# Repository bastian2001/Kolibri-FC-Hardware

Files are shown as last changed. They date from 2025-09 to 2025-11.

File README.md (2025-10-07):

# RP2350 Flight Controller for FPV

This is the hardware part of the Kolibri Flight Controller. Currently there are two versions: A 30mm (V0.5) and a 20mm (V0.6) FC. They are both pretty similar in terms of features, and mostly differ in their form factor and ease of soldering, but also featurewise, they are slightly different. They both feature:

-   3-8S input voltage
-   RP2350 microcontroller
-   2.4GHz ELRS onboard
-   5V 2.5A, 10V 2.5A buck converters
-   Analog character based OSD similar to Betaflight/iNav
-   Barometer (STM LPS22HB)
-   Speaker driver up to VBat

They differ slightly:

-   Gyro: BMI270 (30mm), ICM-42688-P with separate LDO (20mm)
-   ELRS: Gemini with PA/LNA (30mm), only one antenna with no PA/LNA (20mm)
-   Blackbox: SD slot (30mm), 256MiB flash chip (20mm)
-   20mm has a switchable 10V rail, 30mm uses that pin for a current sensor

While the 30mm FC works really well, the 20mm FC is just ordered and completely untested. While most features are a size decision, I will probably phase out the BMI270 and switch over to the ICM-42688-P, and I'd count a switchable 10V rail as more important than a current sensor, so as long as a 2350 is used, I will probably do that in the future, too. An RP235xB (only feasible on 30mm FC) has more pins though and might offer more features down the line, too.

The firmware and configurator can be found [here](https://github.com/bastian2001/Kolibri-FC).

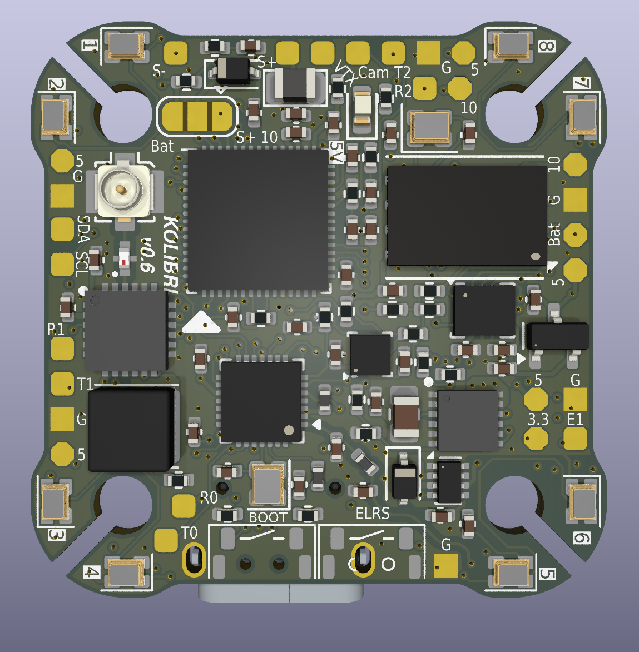
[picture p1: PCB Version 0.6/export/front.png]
Front side of FC

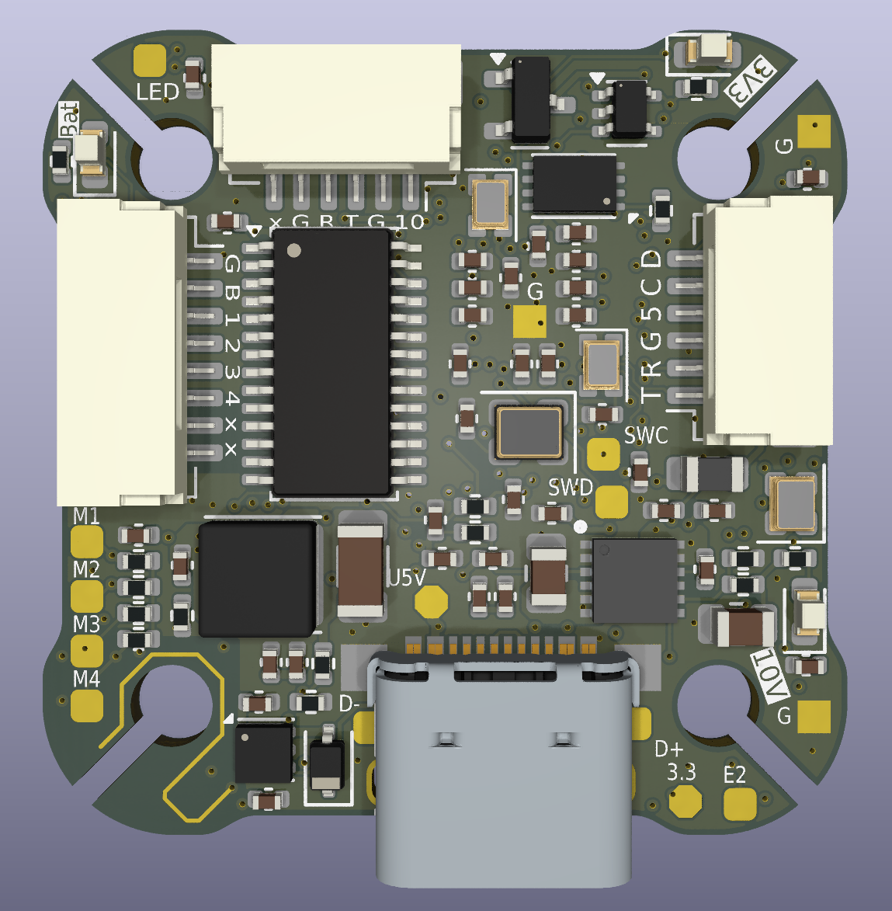
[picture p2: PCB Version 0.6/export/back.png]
Back side of FC


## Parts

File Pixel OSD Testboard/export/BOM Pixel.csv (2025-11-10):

# | Reference | Value | Footprint | Qty
1 | 'C1 | C2 | C3 | C4 | C5 | C6 | C7 | C8 | C9 | C10 | C14 | C15 | C16 | C19 | C20 | C22 | C28 | C45 | C46 | C54 | C56 | C57' | 100n | Capacitor_SMD:C_0402_1005Metric | 22
2 | 'C11 | C12' | 100n | Capacitor_SMD:C_0603_1608Metric_Pad1.08x0.95mm_HandSolder | 2
3 | C13 | 510p | Capacitor_SMD:C_0603_1608Metric_Pad1.08x0.95mm_HandSolder | 1
4 | 'C17 | C18 | C52' | 10u | Capacitor_SMD:C_0603_1608Metric_Pad1.08x0.95mm_HandSolder | 3
5 | 'C21 | C49 | C50 | C55' | 1u | Capacitor_SMD:C_0402_1005Metric | 4
6 | C23 | 10p | Capacitor_SMD:C_0402_1005Metric_Pad0.74x0.62mm_HandSolder | 1
7 | 'C24 | C25 | C26 | C27' | 100n | Capacitor_SMD:C_0402_1005Metric_Pad0.74x0.62mm_HandSolder | 4
8 | 'C29 | C30 | C31 | C32 | C33 | C34 | C35 | C36' | C | Capacitor_SMD:C_0201_0603Metric | 8
9 | 'C37 | C38 | C39 | C40 | C41 | C42 | C43 | C44' | C | Capacitor_SMD:C_0201_0603Metric_Pad0.64x0.40mm_HandSolder | 8
10 | 'C47 | C51' | 10u | Capacitor_SMD:C_0402_1005Metric | 2
11 | C48 | 10u | Capacitor_SMD:C_0603_1608Metric | 1
12 | C53 | 1u | Capacitor_SMD:C_0603_1608Metric_Pad1.08x0.95mm_HandSolder | 1
13 | D1 | 1N4148WS | Diode_SMD:D_SOD-323 | 1
14 | D2 | yellow | LED_SMD:LED_0603_1608Metric | 1
15 | D3 | green | LED_SMD:LED_0603_1608Metric | 1
16 | D4 | red | LED_SMD:LED_0603_1608Metric | 1
17 | D5 | SL16 | Diode_SMD:D_SOD-123 | 1
18 | J1 | USB_C_Receptacle_USB2.0_16P | Kolibri custom:USB-C SMD+THT | 1
19 | L1 | 10u | Inductor_SMD:L_0805_2012Metric | 1
20 | 'P1 | P2 | P3 | P4 | P5 | P6 | P7 | P8' | ~ | Kolibri custom:Solder_Pad_rounded | 8
21 | 'P9 | P10 | P11 | P12 | P13 | P14' | ~ | Kolibri custom:Solder_Pad_octa | 6
22 | 'P15 | P16 | P17 | P18' | ~ | Kolibri custom:Solder_Pad_rect | 4
23 | Q1 | 2SK3019 | Package_TO_SOT_SMD:SOT-523 | 1
24 | 'R1 | R2' | 5.1k | Resistor_SMD:R_0402_1005Metric | 2
25 | 'R3 | R4' | 27 | Resistor_SMD:R_0402_1005Metric | 2
26 | R5 | 680 | Resistor_SMD:R_0603_1608Metric_Pad0.98x0.95mm_HandSolder | 1
27 | R6 | 620 | Resistor_SMD:R_0603_1608Metric_Pad0.98x0.95mm_HandSolder | 1
28 | 'R7 | R9 | R11 | R13' | 33k | Resistor_SMD:R_0402_1005Metric_Pad0.72x0.64mm_HandSolder | 4
29 | 'R8 | R10 | R12 | R14' | 100k | Resistor_SMD:R_0402_1005Metric_Pad0.72x0.64mm_HandSolder | 4
30 | 'R15 | R39' | 1k | Resistor_SMD:R_0402_1005Metric | 2
31 | 'R16 | R27 | R36' | 10k | Resistor_SMD:R_0402_1005Metric | 3
32 | R18 | 100 | Resistor_SMD:R_0603_1608Metric_Pad0.98x0.95mm_HandSolder | 1
33 | 'R19 | R20' | 100k | Resistor_SMD:R_0603_1608Metric_Pad0.98x0.95mm_HandSolder | 2
34 | 'R22 | R23 | R24 | R25 | R26 | R43 | R44' | 1k | Resistor_SMD:R_0603_1608Metric_Pad0.98x0.95mm_HandSolder | 7
35 | 'R28 | R29' | 75 | Resistor_SMD:R_0402_1005Metric | 2
36 | 'R32 | R33' | 100k | Resistor_SMD:R_0402_1005Metric | 2
37 | R34 | 47k | Resistor_SMD:R_0402_1005Metric | 1
38 | R35 | 15k | Resistor_SMD:R_0402_1005Metric | 1
39 | 'R37 | R38' | 470 | Resistor_SMD:R_0402_1005Metric | 2
40 | R40 | 1M | Resistor_SMD:R_0603_1608Metric_Pad0.98x0.95mm_HandSolder | 1
41 | R41 | 2.2M | Resistor_SMD:R_0603_1608Metric_Pad0.98x0.95mm_HandSolder | 1
42 | R42 | 390k | Resistor_SMD:R_0603_1608Metric_Pad0.98x0.95mm_HandSolder | 1
43 | SW1 | ~ | Kolibri custom:Button C530669 | 1
44 | 'TP1 | TP2 | TP3 | TP4 | TP5 | TP6 | TP8 | TP9 | TP10' | TestPoint_Probe | TestPoint:TestPoint_Pad_D1.0mm | 9
45 | U1 | RP2040 | Package_DFN_QFN:QFN-56-1EP_7x7mm_P0.4mm_EP3.2x3.2mm | 1
46 | U2 | LM1881 | Package_SO:SOIC-8_3.9x4.9mm_P1.27mm | 1
47 | U3 | W25Q16JVSS | Package_SO:SOIC-8_5.3x5.3mm_P1.27mm | 1
48 | U4 | Opamp_Quad | Package_SO:TSSOP-14_4.4x5mm_P0.65mm | 1
49 | U5 | 74LVC1G66 | Package_TO_SOT_SMD:SOT-353_SC-70-5 | 1
50 | 'U6 | U10' | FSA3157P6X | Package_TO_SOT_SMD:SOT-363_SC-70-6 | 2
51 | U7 | TMUX1308DYY | Package_SO:Texas_DYY0016A_TSOT-23-16_2x4.2mm_P0.5mm | 1
52 | U8 | LGS5145 | Package_TO_SOT_SMD:SOT-23-6 | 1
53 | U9 | C19631737 | Package_TO_SOT_SMD:SOT-23-3 | 1
54 | U11 | OPA188xxDBV | Package_TO_SOT_SMD:TSOT-23-5 | 1
55 | Y1 | ASE-xxxMHz | Oscillator:Oscillator_SMD_Abracon_ASE-4Pin_3.2x2.5mm_HandSoldering | 1

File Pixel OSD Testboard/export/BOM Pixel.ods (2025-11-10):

# | Reference | Value | Footprint | Qty | LCSC # |  | Order # | Order Qty
1 | C1,C2,C3,C4,C5,C6,C7,C8,C9,C10,C14,C15,C16,C19,C20,C22,C28,C45,C46,C54,C56,C57 | 100n | Capacitor_SMD:C_0402_1005Metric | 22 | generic |  |  | 0
2 | C11,C12 | 100n | Capacitor_SMD:C_0603_1608Metric_Pad1.08x0.95mm_HandSolder | 2 | generic |  |  | 0
3 | C13 | 510p | Capacitor_SMD:C_0603_1608Metric_Pad1.08x0.95mm_HandSolder | 1 | generic |  | C20069830 | 100
4 | C17,C18,C52 | 10u | Capacitor_SMD:C_0603_1608Metric_Pad1.08x0.95mm_HandSolder | 3 | generic |  |  | 0
5 | C21,C49,C50,C55 | 1u | Capacitor_SMD:C_0402_1005Metric | 4 | generic |  |  | 0
6 | C23 | 10p | Capacitor_SMD:C_0402_1005Metric_Pad0.74x0.62mm_HandSolder | 1 | generic |  |  | 0
7 | C24,C25,C26,C27 | 100n | Capacitor_SMD:C_0402_1005Metric_Pad0.74x0.62mm_HandSolder | 4 | generic |  |  | 0
8 | C29,C30,C31,C32,C33,C34,C35,C36 | C | Capacitor_SMD:C_0201_0603Metric | 8 | generic test only |  | C7393836 | 100
9 | C37,C38,C39,C40,C41,C42,C43,C44 | C | Capacitor_SMD:C_0201_0603Metric_Pad0.64x0.40mm_HandSolder | 8 | generic test only |  | C7393836 | 0 | see above
10 | C47,C51 | 10u | Capacitor_SMD:C_0402_1005Metric | 2 | generic |  |  | 0
11 | C48 | 10u | Capacitor_SMD:C_0603_1608Metric | 1 | generic |  |  | 0
12 | C53 | 1u | Capacitor_SMD:C_0603_1608Metric_Pad1.08x0.95mm_HandSolder | 1 | generic |  |  | 0
13 | D1 | 1N4148WS | Diode_SMD:D_SOD-323 | 1 | generic |  |  | 0
14 | D2 | yellow | LED_SMD:LED_0603_1608Metric | 1 | generic |  |  | 0
15 | D3 | green | LED_SMD:LED_0603_1608Metric | 1 | generic |  |  | 0
16 | D4 | red | LED_SMD:LED_0603_1608Metric | 1 | generic |  |  | 0
17 | D5 | SL16 | Diode_SMD:D_SOD-123 | 1 | generic |  |  | 0
18 | J1 | USB_C_Receptacle_USB2.0_16P | Kolibri custom:USB-C SMD+THT | 1 | C963217 |  |  | 0
19 | L1 | 10u | Inductor_SMD:L_0805_2012Metric | 1 | generic 400mA |  | C285963 | 50
20 | P1,P2,P3,P4,P5,P6,P7,P8 | ~ | Kolibri custom:Solder_Pad_rounded | 8 | - |  |  | -
21 | P9,P10,P11,P12,P13,P14 | ~ | Kolibri custom:Solder_Pad_octa | 6 | - |  |  | -
22 | P15,P16,P17,P18 | ~ | Kolibri custom:Solder_Pad_rect | 4 | - |  |  | -
23 | Q1 | 2SK3019 | Package_TO_SOT_SMD:SOT-523 | 1 | generic, e.g. C41409350 |  | C41409350 | 50
24 | R1,R2 | 5.1k | Resistor_SMD:R_0402_1005Metric | 2 | generic 1% |  |  | 0
25 | R3,R4 | 27 | Resistor_SMD:R_0402_1005Metric | 2 | generic 1% |  |  | 0
26 | R5 | 680 | Resistor_SMD:R_0603_1608Metric_Pad0.98x0.95mm_HandSolder | 1 | generic 1% |  | C3016261 | 100
27 | R6 | 620 | Resistor_SMD:R_0603_1608Metric_Pad0.98x0.95mm_HandSolder | 1 | generic 1% |  | C49653145 | 100
28 | R7,R9,R11,R13 | 33k | Resistor_SMD:R_0402_1005Metric_Pad0.72x0.64mm_HandSolder | 4 | generic 1% |  |  | 0
29 | R8,R10,R12,R14 | 100k | Resistor_SMD:R_0402_1005Metric_Pad0.72x0.64mm_HandSolder | 4 | generic 1% |  |  | 0
30 | R15,R39 | 1k | Resistor_SMD:R_0402_1005Metric | 2 | generic 1% |  |  | 0
31 | R16,R27,R36 | 10k | Resistor_SMD:R_0402_1005Metric | 3 | generic 1% |  |  | 0
32 | R18 | 100 | Resistor_SMD:R_0603_1608Metric_Pad0.98x0.95mm_HandSolder | 1 | generic 1% |  |  | 0
33 | R19,R20 | 100k | Resistor_SMD:R_0603_1608Metric_Pad0.98x0.95mm_HandSolder | 2 | generic 1% |  |  | 0
34 | R22,R23,R24,R25,R26,R43,R44 | 1k | Resistor_SMD:R_0603_1608Metric_Pad0.98x0.95mm_HandSolder | 7 | generic 1% |  |  | 0
35 | R28,R29 | 75 | Resistor_SMD:R_0402_1005Metric | 2 | generic 1% |  |  | 0
36 | R32,R33 | 100k | Resistor_SMD:R_0402_1005Metric | 2 | generic 1% |  |  | 0
37 | R34 | 47k | Resistor_SMD:R_0402_1005Metric | 1 | generic 1% |  |  | 0
38 | R35 | 15k | Resistor_SMD:R_0402_1005Metric | 1 | generic 1% |  |  | 0
39 | R37,R38 | 470 | Resistor_SMD:R_0402_1005Metric | 2 | generic 1% |  |  | 0
40 | R40 | 1M | Resistor_SMD:R_0603_1608Metric_Pad0.98x0.95mm_HandSolder | 1 | generic 1% |  | C2907003 | 100
41 | R41 | 2.2M | Resistor_SMD:R_0603_1608Metric_Pad0.98x0.95mm_HandSolder | 1 | generic 1% |  | C48391814 | 100
42 | R42 | 390k | Resistor_SMD:R_0603_1608Metric_Pad0.98x0.95mm_HandSolder | 1 | generic 1% |  | C163911 | 100
43 | SW1 | ~ | Kolibri custom:Button C530669 | 1 | generic, e.g. C530669 |  |  | 0
44 | TP1,TP2,TP3,TP4,TP5,TP6,TP8,TP9,TP10 | TestPoint_Probe | TestPoint:TestPoint_Pad_D1.0mm | 9 | - |  |  | -
45 | U1 | RP2040 | Package_DFN_QFN:QFN-56-1EP_7x7mm_P0.4mm_EP3.2x3.2mm | 1 | C2040 |  |  | 0
46 | U2 | LM1881 | Package_SO:SOIC-8_3.9x4.9mm_P1.27mm | 1 | C518922 |  | C518922 | 2
47 | U3 | W25Q16JVSS | Package_SO:SOIC-8_5.3x5.3mm_P1.27mm | 1 | C131025, C82317 |  |  | 0
48 | U4 | Opamp_Quad | Package_SO:TSSOP-14_4.4x5mm_P0.65mm | 1 | C7463388 |  | C7463388 | 10
49 | U5 | 74LVC1G66 | Package_TO_SOT_SMD:SOT-353_SC-70-5 | 1 | C46553571 |  | C46553571 | 20
50 | U6,U10 | FSA3157P6X | Package_TO_SOT_SMD:SOT-363_SC-70-6 | 2 | C41431789 |  | C41431789 | 10
51 | U7 | TMUX1308DYY | Package_SO:Texas_DYY0016A_TSOT-23-16_2x4.2mm_P0.5mm | 1 | C2877584 |  | C2877584 | 5
52 | U8 | LGS5145 | Package_TO_SOT_SMD:SOT-23-6 | 1 | C5123971 |  | C5123971 | 5
53 | U9 | C19631737 | Package_TO_SOT_SMD:SOT-23-3 | 1 | C19631737 |  | C19631737 | 50
54 | U11 | OPA188xxDBV | Package_TO_SOT_SMD:TSOT-23-5 | 1 | C7463385 |  | C7463385 | 5
55 | Y1 | ASE-xxxMHz | Oscillator:Oscillator_SMD_Abracon_ASE-4Pin_3.2x2.5mm_HandSoldering | 1 |  |  |  | 0
 |  |  |  |  |  |  |  | -
 |  |  |  |  |  |  |  | -
 | FC V0.6 Order: | order will be combined, ignore for Pixel PCB |  |  |  |  |  | -
1 | C1,C3,C4,C5,C6,C7,C8,C9,C10,C16,C17,C18,C19,C20,C21,C23,C24,C27,C28,C30,C34,C40,C44,C45,C46,C48,C56,C65,C67,C70,C71,C76,C85,C86 | 100n | Capacitor_SMD:C_0402_1005Metric | 34 | generic |  |  | 0
2 | C2,C11,C12,C13 | 4.7u | Capacitor_SMD:C_0402_1005Metric | 4 | generic |  |  | 0
3 | C14,C15,C38,C39,C79,C80 | 15p | Capacitor_SMD:C_0402_1005Metric | 6 | generic NP0 |  |  | 0
4 | C22 | 2.2u | Capacitor_SMD:C_0402_1005Metric | 1 | generic |  | C12530 | 100
5 | C25,C42,C43,C87 | 10n | Capacitor_SMD:C_0402_1005Metric | 4 | generic |  |  | 0
6 | C26,C29,C33,C35,C63,C64,C73,C81,C83,C84 | 1u | Capacitor_SMD:C_0402_1005Metric | 10 | generic |  |  | 0
7 | C31,C36,C77,C78,C88 | 10u | Capacitor_SMD:C_0402_1005Metric | 5 | generic |  |  | 0
8 | C32,C37 | 1.5p | Capacitor_SMD:C_0402_1005Metric | 2 | generic NP0 |  |  | 0
9 | C41 | 470n | Capacitor_SMD:C_0402_1005Metric | 1 | generic |  |  | 0
10 | C66 | 47u | Capacitor_SMD:C_1206_3216Metric | 1 | generic 10V+ |  |  | 0
11 | C68,C69 | 4.7u | Capacitor_SMD:C_0805_2012Metric | 2 | generic 50V+ |  | C2903668 | 50
12 | C72 | 22u | Capacitor_SMD:C_0805_2012Metric | 1 | generic 25V+ |  |  | 0
13 | D1,D2,D3,D4,D5,D6,D7,D8,D9,D11 | ~ | Kolibri custom:WS2812B_1615 | 10 | generic |  |  | 0
14 | D10,D12,D13 | 1N4148WS | Diode_SMD:D_SOD-323 | 3 | generic |  |  | 0
15 | D14 | red | LED_SMD:LED_0603_1608Metric | 1 | generic |  |  | 0
16 | D15 | violet | LED_SMD:LED_0603_1608Metric | 1 | generic |  |  | 0
17 | D16 | blue | LED_SMD:LED_0603_1608Metric | 1 | generic |  |  | 0
18 | D17 | green | LED_SMD:LED_0603_1608Metric | 1 | generic |  |  | 0
19 | FL1 | 2450FM07D0034T | SamacSys_Parts:2450FM07D0034T | 1 | C2917726, C6054595, C2651081 |  | C2651081 | 30
20 | IC1 | SX1280IMLTRT | SamacSys_Parts:QFN50P400X400X100-25N-D | 1 | C2151551 |  | C2151551 | 10
21 | IC5,IC6 | LMR38025SDRRR | SamacSys_Parts:SON50P300X300X80-13N | 2 | C22405313 |  |  | 0
22 | J1 | USB_C_Receptacle_USB2.0_16P | Kolibri custom:USB-C SMD+THT | 1 | C963217 |  |  | 0
23 | J3 | Conn_Coaxial_Small | Connector_Coaxial:U.FL_Molex_MCRF_73412-0110_Vertical | 1 | C5137195 |  |  | 0
24 | J5 | Conn_01x08_MountingPin | Connector_JST:JST_SH_SM08B-SRSS-TB_1x08-1MP_P1.00mm_Horizontal | 1 | generic, e.g. C7433429 |  |  | 0
25 | J6,J7 | Conn_01x06_MountingPin | Connector_JST:JST_SH_SM06B-SRSS-TB_1x06-1MP_P1.00mm_Horizontal | 2 | generic, e.g. C2688763 |  |  | 0
26 | L1 | 3.3u | Kolibri custom:Abracon AOTA 0806 | 1 | C42411119 |  |  | 0
27 | L2 | 2.0n | Inductor_SMD:L_0402_1005Metric | 1 | generic for RF |  |  | 0
28 | L3 | 3.0n | Inductor_SMD:L_0402_1005Metric | 1 | generic for RF |  |  | 0
29 | L4 | 24n | Inductor_SMD:L_0402_1005Metric | 1 | generic |  |  | 0
30 | L5 | 15u | Inductor_SMD:L_0805_2012Metric | 1 | generic |  |  | 0
31 | L7,L8 | 4.7u | Inductor_SMD:L_Cenker_CKCS4020 | 2 | generic, e.g. C520275 |  |  | 0
32 | P1,P2,P3,P4,P5,P6,P7,P8,P9,P10,P11,P12,P13,P16,P17,P18,P19,P20,P21,P35,P36,P37,P38 | ~ | Kolibri custom:Solder_Pad_rounded | 23 | - |  |  | -
33 | P14,P22,P23,P24,P26,P27,P40,P42,P43 | ~ | Kolibri custom:Solder_Pad_rect | 9 | - |  |  | -
34 | P15,P25,P28,P29,P30,P31,P32,P33,P34,P39,P41 | ~ | Kolibri custom:Solder_Pad_octa | 11 | - |  |  | -
35 | Q1 | BSS138 | Package_TO_SOT_SMD:SOT-23 | 1 | generic |  |  | 0
36 | R1,R2 | 27 | Resistor_SMD:R_0402_1005Metric | 2 | generic 1% |  |  | 0
37 | R3 | 33 | Resistor_SMD:R_0402_1005Metric | 1 | generic 1% |  |  | 0
38 | R4,R21,R22,R23,R30,R33 | 1k | Resistor_SMD:R_0402_1005Metric | 6 | generic 1% |  |  | 0
39 | R5,R6 | 5.1k | Resistor_SMD:R_0402_1005Metric | 2 | generic 1% |  |  | 0
40 | R7,R8,R34,R35,R36,R37 | 6.8k | Resistor_SMD:R_0402_1005Metric | 6 | generic 1% |  |  | 0
41 | R9,R10,R16,R20,R27 | 10k | Resistor_SMD:R_0402_1005Metric | 5 | generic 1% |  |  | 0
42 | R13,R26 | 100k | Resistor_SMD:R_0402_1005Metric | 2 | generic 1% |  |  | 0
43 | R14 | 39k | Resistor_SMD:R_0402_1005Metric | 1 | generic 1% |  |  | 0
44 | R15 | 40.2k | Resistor_SMD:R_0402_1005Metric | 1 | generic 1% |  |  | 0
45 | R17 | 22.6k | Resistor_SMD:R_0402_1005Metric | 1 | generic 1% |  |  | 0
46 | R18 | 21.5k | Resistor_SMD:R_0402_1005Metric | 1 | generic 1% |  |  | 0
47 | R19 | 90.9k | Resistor_SMD:R_0402_1005Metric | 1 | generic 1% |  |  | 0
48 | R24,R25 | 75 | Resistor_SMD:R_0402_1005Metric | 2 | generic 1% |  |  | 0
49 | R28 | 8.2k | Resistor_SMD:R_0402_1005Metric | 1 | generic 1% |  |  | 0
50 | R29 | 3.3k | Resistor_SMD:R_0402_1005Metric | 1 | generic 1% |  |  | 0
51 | R31 | 2.2k | Resistor_SMD:R_0402_1005Metric | 1 | generic 1% |  |  | 0
52 | R41 | 22k | Resistor_SMD:R_0402_1005Metric | 1 | generic 1% |  |  | 0
53 | SW1,SW2 | ~ | Kolibri custom:Button C530669 wo holes | 2 | generic, e.g. C530669 |  |  | 0
54 | U1 | RP2350A | Kolibri custom:QFN-60_EP_7x7_Pitch0.4mm | 1 | C42411118 |  |  | 0
55 | U2 | C5250982 | Package_TO_SOT_SMD:SOT-23 | 1 | Generic 1.8V, 70dB, e.g. C5250982 |  | C5250982 | 50
56 | U3 | ESP8685-H4 | Package_DFN_QFN:QFN-28-1EP_4x4mm_P0.4mm_EP2.4x2.4mm | 1 | C4944062 |  | C4944062 | 5
57 | U4 | TPS2116DRL | Package_TO_SOT_SMD:SOT-583-8 | 1 | C22399676, C3235557 |  |  | 0
58 | U5 | AT7456E | Package_SO:HTSSOP-28-1EP_4.4x9.7mm_P0.65mm_EP2.75x6.2mm | 1 | C82351 |  |  | 0
59 | U6 | MT29F2G01ABAGDWB-IT:G | Package_SON:WSON-8-1EP_8x6mm_P1.27mm_EP3.4x4.3mm | 1 | C410863 |  | C410863 | 2
60 | U7 | TPS746-3.3DRV | Package_SON:WSON-6-1EP_2x2mm_P0.65mm_EP1x1.6mm | 1 | C2846784 |  |  | 0
61 | U8 | C3029047 | Package_TO_SOT_SMD:SOT-353_SC-70-5 | 1 | generic LMV321. e.g. C3029047 |  | C3029047 | 10
62 | U10 | W25Q16JVUXIQ | Package_SON:Winbond_USON-8-1EP_3x2mm_P0.5mm_EP0.2x1.6mm | 1 | C2843335 |  |  | 0
63 | U11 | LPS22HB | Package_LGA:ST_HLGA-10_2x2mm_P0.5mm_LayoutBorder3x2y | 1 | C94049 |  |  | 0
64 | U12 | ICM-42688-P | Package_LGA:LGA-14_3x2.5mm_P0.5mm_LayoutBorder3x4y | 1 | C1850418 |  | C1850418 | 0
65 | Y1 | Crystal_GND24 | Crystal:Crystal_SMD_2520-4Pin_2.5x2.0mm | 1 | generic 12 Mhz, e.g. C7294610 |  |  | 0
66 | Y2,Y4,Y5 | Crystal_GND24 | Crystal:Crystal_SMD_2016-4Pin_2.0x1.6mm | 3 | generic, 27MHz e.g. C18214311, 52MHz e.g. C3034316, 40MHz e.g.C37635335 | 27 | C18214311 | 0
 |  |  |  |  |  | 52 | C3034316 | 0
 |  |  |  |  |  | 40 | C37635335 | 0
 |  |  |  |  |  | 52 TCXO | C22434896 | 10

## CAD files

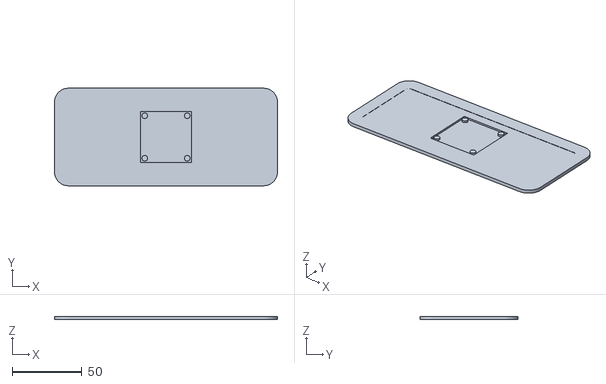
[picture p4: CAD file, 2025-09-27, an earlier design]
deprecated/PCB Version 0.1/Solder rig/Alignment card.stl
160.0 x 70.0 x 2.40

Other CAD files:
PCB Version 0.1/Solder rig/Alignment card.prt
deprecated/PCB Version 0.1/Solder rig/Alignment card.prt

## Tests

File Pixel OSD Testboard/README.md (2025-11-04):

# Goal of this board

I want to implement a pixel OSD in some future FC version. Because I am very unsure about how PAL/NTSC work, I want to test all of the hardware on a separate, cheap and easily debuggable, board first. It has a bunch of components that I want to remove later on, and that are just for debugging (thus making it larger than it needs to be). Furthermore, some of the hardware is chosen purely because I have it laying around (e.g. RP2040 instead of RP2350), so I get rid of old stock.

Pixel OSD will have multiple advantages

-   Drawing graphs and free shapes
-   varying font size and grid
-   cheaper
-   shades of grey (hopefully)
-   optional: remove grey, save one pin compared to MAX (hopefully)

This board is only a proof of concept. I'll try to put it into my quad during flight, but in the end it will be implemented on the main FC. Thus, it will likely only support a character based OSD, so it doesn't require a whole rewrite of the FC firmware for now: The interface is Serial/UART with MSP Displayport. Yes, hopefully this can give us a higher character count on regular analog video (to some extent, because the resolution is already close to its limit)

## Stuff that will be removed later on

-   Maybe I can buffer a bit less: 1-2 op amp channels could go?
-   Are all 100nF caps needed?
-   video LPF on LM1881 input?
-   Virtual white and the white selector: White should just come from the peak detector
-   Some components for lines like VSync: I want to use only composite sync
-   RP2040/LDO/LED/USB: Will be integrated into main RP2350 instead of MAX7456E

## How it works

How the hardware works is commented on the sheet.

The software will use PIO to detect sync pulses, then use DMA to feed a pixel buffer into the PIO which then outputs the data, timed correctly. PIO has the advantage of not needing super precise interrupt timing, because the coprocessor is very precise time-wise by definition.

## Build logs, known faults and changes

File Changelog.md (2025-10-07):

## Design errors, fixes and improvements between PCB revisions

### V0.1

-   Known issues:
    1. Current Sensor
        - If there is no current sensor wire attached, the INA139 will output 4.3V, killing the ADC and potentially the Microcontroller
        - Solution: Wire a pullup resistor from the C pad to the V+ pad to ensure that the measured current is 0 rather than infinity when there is nothing attached to the C pad.
    2. Buck Converters
        - A diode is misplaced, killing the buck converters
        - Solution: Place the diode in the correct spot on both bucks
    3. Oscillators
        - There is only a spot for crystals but not for their capacitors, and the wiring is wrong for use with oscillators
        - Solution: Change wiring for oscillator for the RP2040
    4. No pullup on the CS line for the flash
    5. Boot button flipped

### V0.2

-   Goal: A working PCB with some tests to make v0.3 the first final version
    -   It uses the same stencil as v0.1, hence I had to make some compromises with regards to routing and other best practices. I didn't want to spend another 15$ on a stencil, when PCBs are so cheap in comparison.
-   Fixes for all 5 problems with v0.1
-   Same stencil
-   Improvements:
    -   0402 solder bridges instead of 0603
    -   8 layers because that allows for free ENIG finish and POFV at JLCPCB
    -   put baro I2C on aux I2C of gyro? => Solder bridge to test this out

### V0.3

-   Goal: V0.2 (and from a purely flying performance perspective v0.1 too) was generally working very well. Goal is to put in some new features especially blackbox on the SD card due to the slow flash writing. Since the microSD has its own buffer, it should be much faster.
-   Improvements
    -   ELRS with true diversity built in
    -   SD card slot for blackbox
    -   new SPI barometer (Goertek SPL06-001)
    -   synchronous buck converters: smaller (, more efficient)
-   Fixes
    -   removed pullup on current sensor (A relic from the INA139)
-   Known issues
    -   100nF 0402 caps on the bottom layer are very close to each other, causing solder bridges - no issue but not ideal
    -   WiFi antenna poor range (5-10 cm), not sure why
    -   ELRS boot pad is hard to reach
    -   SX1281 crystals 90 degrees rotated --> SX1281 doesn't work at all (jank fix works)
    -   forgot I2C pullups. No issue rn (no sensors using I2C), but with a compass it might be
    -   Bad ELRS range --> a few possible reasons
        -   LNA not working --> most likely (yet reason still unknown), because the RSSI has a very fast jump from about -25 to -75dBm, indicating something else than a pure passives issue. Also, in the transmission path (telemetry), everything works fine, indicating that the PCB and passive components are fine in general
        -   pads grounded insufficiently --> my bad, I didn't compare the library footprint with the datasheet, some pads are not grounded, as they were marked NC in the library but GND in the datasheet --> I put a solder bridge on the pads that are not grounded, and still it doesn't work well, so still unlikely
        -   AT2401C just not working? --> unlikely, but maybe there's a difference between this clone and the RFX2401C
        -   All of them are pretty unlikely, given the weird jump, but I don't know what else it could be
    -   OSD crystal somewhat weird. Nothing I tried worked. I tried putting a crystal from a brand new off the shelf FC on it, as well as using a crystal from V0.2 (via separate wires), as well as changing various components like the AT7456E or capacitors. Sometimes (with the off-the-shelf crystal or the V0.2 crystal), I get video for like 20-60 seconds, but after a while they all stop working until I cut power and wait a few seconds. Nothing gets particularly warm, hence my confusion with the issue. Will go back to the design that worked in V0.2, to give me some space to play with all different sizes

### V0.4

-   Goal: V0.3 introduced a lot of new features, but not all work properly. This PCB will hopefully fix all the new issues that emerged with V0.3. Especially the ELRS range and the OSD crystal, but also implement a proper non-jank fixes for the other stuff. No new features, similar to V0.2 compared to V0.1. Biggest issue is that this time I cannot really explain to myself the two big issues and so I just have to guess.
-   Fixes (at least I hope)
    -   ELRS range -> Test RFX2401C instead of AT2401C, and ground all the pins. I will also swap the RFX2401C onto V0.3 after arrival to see if it's a PCB issue or a component issue
    -   ELRS WiFi -> proper filter according to datasheet
    -   ELRS crystal 90° rotated
    -   ELRS boot pad is now a button
    -   A pair of 4.7kOhm pullups for I2C
    -   OSD crystal -> back to V0.2 design, except with more possibilities of testing, like selectable voltage and selectable whether a crystal or oscillator is used
    -   slightly more spacing for 100nF caps on the bottom layer

### V0.5

-   Changes
    -   Switch to RP2350
    -   some changes to the ELRS receiver, maybe it'll work this time?
    -   First version designed in KiCad
    -   Bus layout changed:
        -   Dedicated 3-wire SPI for gyro (PIO) => DMA polling should be possible now
        -   baro has one I2C with external devices like compass
        -   SDIO for SD card (PIO)
        -   Dedicated SPI for OSD
    -   WS2812 LEDs for the swag
    -   better speaker driver
-   What works: Seemingly everything :tada:
-   Idea dump for future:
    -   Reorder 6 pin for GPS/compass: Currently not immediately compatible with Walksnail M10 (RX/TX and SDA/SCL need to be swapped)
    -   RP235xB: more pins for
        -   normal LEDs again
        -   full duplex spi to gyro
        -   separate external I2C for compass
        -   baro via SPI instead of I2C (together with OSD)
        -   more UARTs via PIO (once SPI is separated, pio2 is completely free)
        -   PWM outputs
    -   Speaker driver with optional 5V input for bench testing or in general
    -   more capacitance on 10V rail
    -   separate gyro LDO, or LPF on its supply
    -   custom pixel OSD using PIO/HSTX :thinking:
    -   possible space savings
        -   smaller crystals
        -   2354 instead of 2350 (no separate flash required)
        -   replace USB on SH plug with solder pads [optionally under the USB port]
        -   (pixel OSD instead of AT7456E)

### V0.6

-   Changes compared to V0.5
    -   ELRS
        -   from TD with PA/LNA to single without PA/LNA
        -   from ESP32 to ESP8685 (C3)
        -   No more separate LDO
    -   Gyro from BMI270 to ICM-42688-P with external clock
    -   Blackbox from SD slot to 2GBit flash chip
    -   Separate gyro LDO (1.8V – let's experiment!)
    -   USB
        -   remove JST header in favor of solder pads
        -   remove TVS
    -   shrink Crystal footprints
    -   replace current sensor pin with 10V reg switch

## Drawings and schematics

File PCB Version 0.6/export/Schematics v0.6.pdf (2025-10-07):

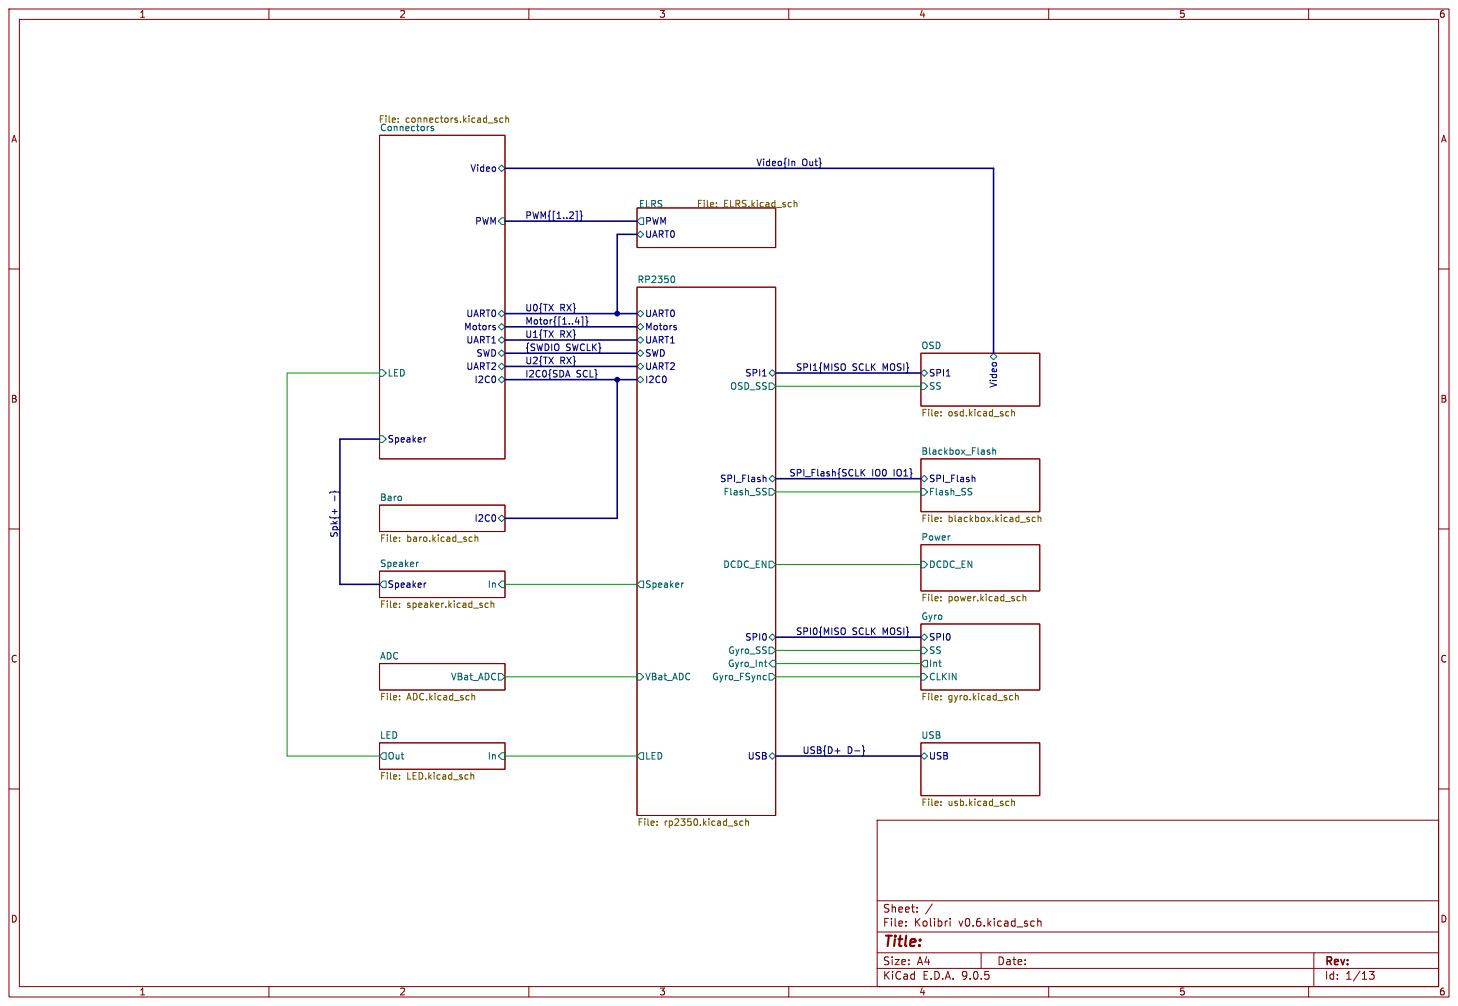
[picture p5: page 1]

Motor{[1..4]}
{SWDIO SWCLK}
SPI_Flash Blackbox_Flash File: blackbox.kicad_sch U2{TX RX}
I2C0{SDA SCL}

Id: 1/13 Title: File: Kolibri v0.6.kicad_sch Sheet: /DCDC_EN

Int CLKIN Gyro File: gyro.kicad_sch

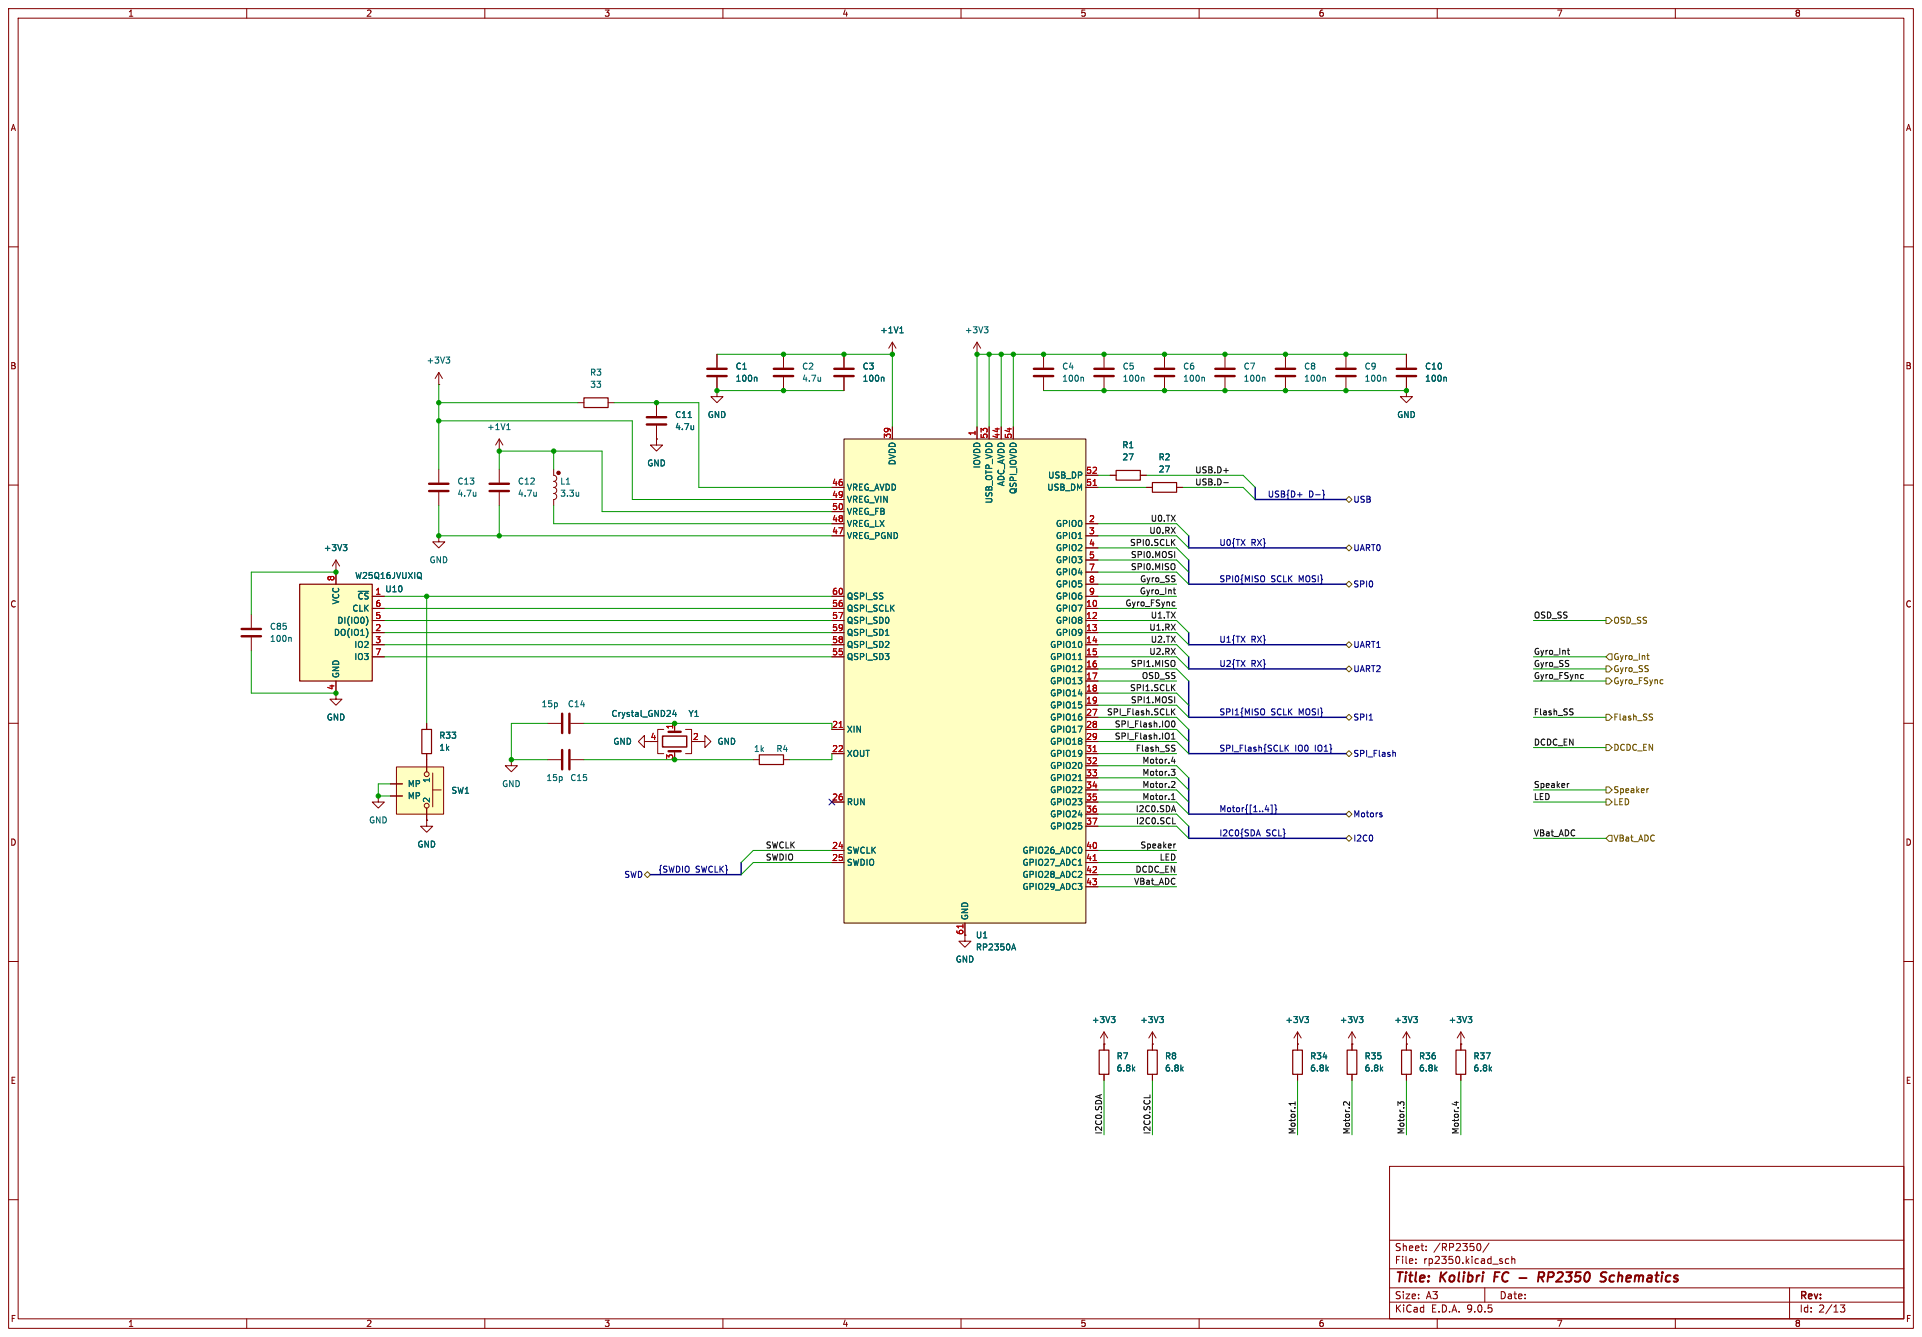
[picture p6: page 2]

File: rp2350.kicad_sch Sheet: /RP2350/
Id: 2/13 Title: Kolibri FC - RP2350 Schematics

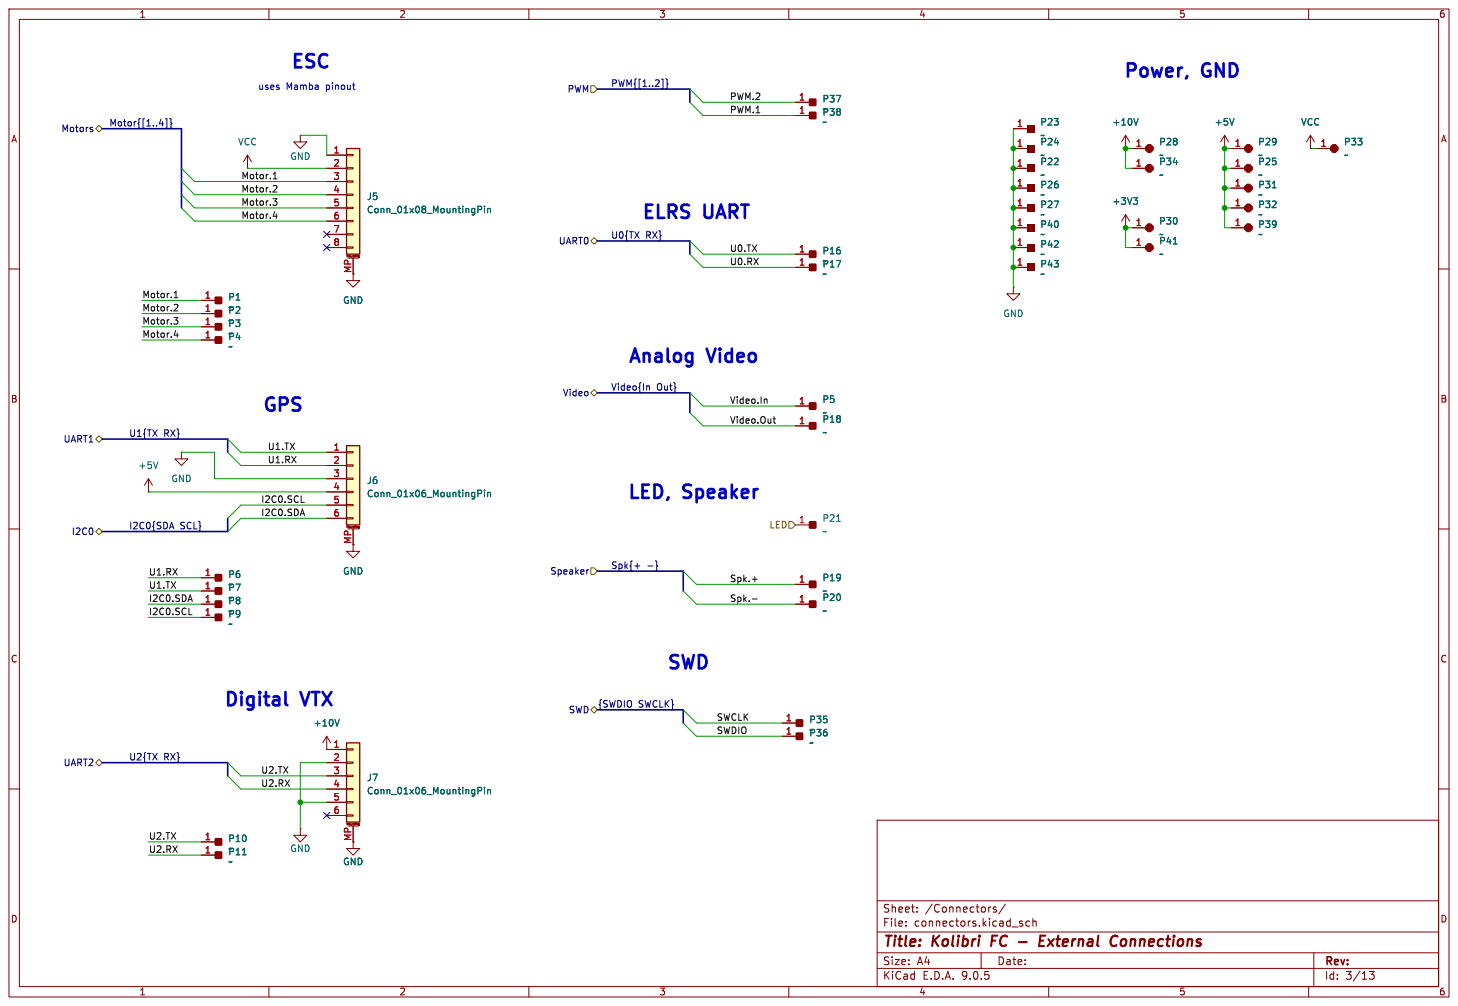
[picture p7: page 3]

Spk.+ Motor.1 Motor.2 Motor.3

File: connectors.kicad_sch Sheet: /Connectors/
Id: 3/13 Title: Kolibri FC - External Connections

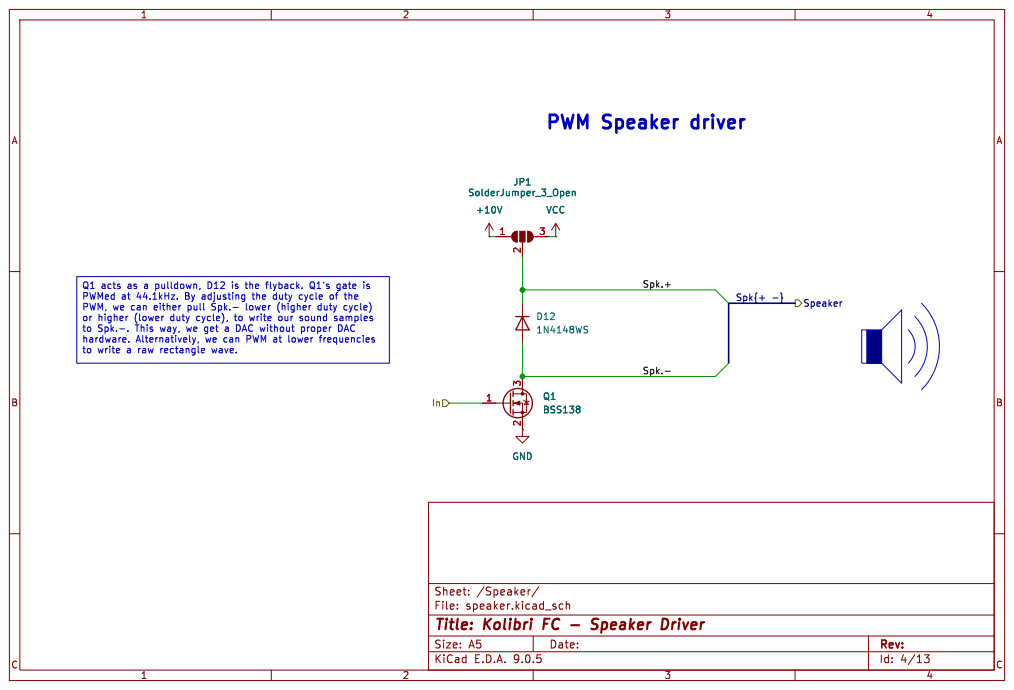
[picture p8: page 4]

JP1 SolderJumper_3_Open

Id: 4/13 Title: Kolibri FC - Speaker Driver File: speaker.kicad_sch Sheet: /Speaker/ 1

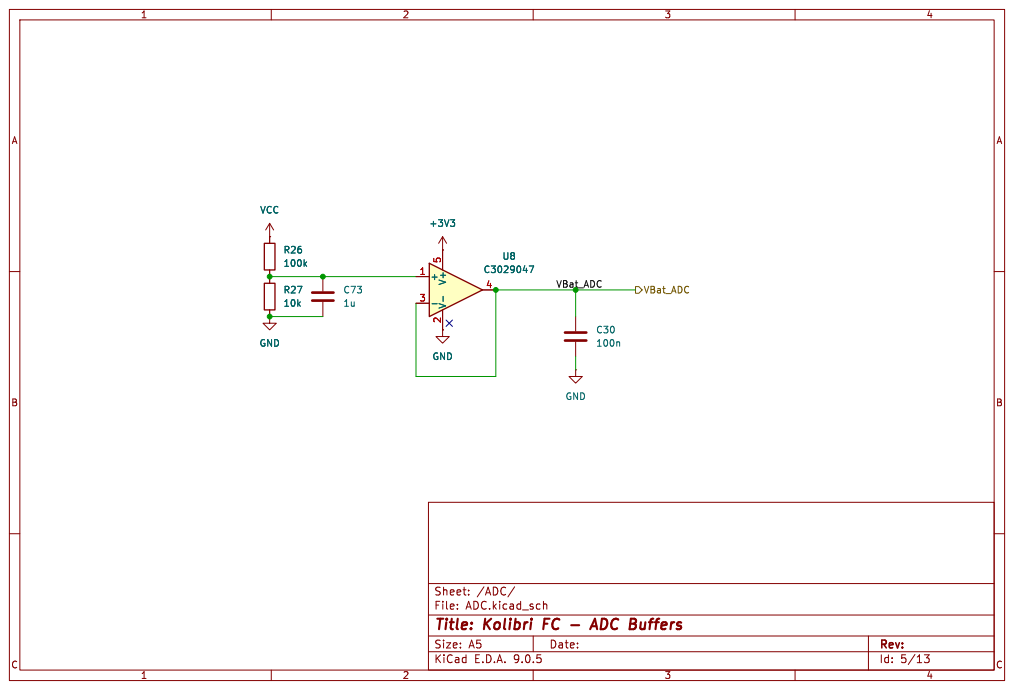
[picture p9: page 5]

Id: 5/13 Title: Kolibri FC - ADC Buffers

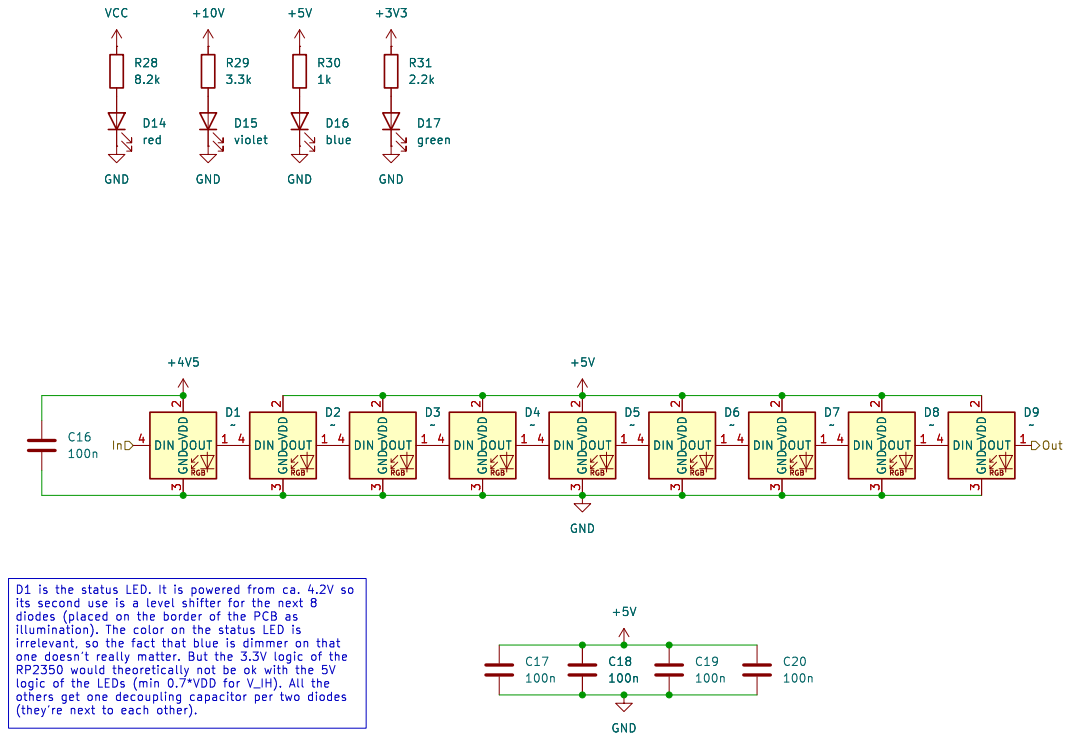
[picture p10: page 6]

its second use is a level shifter for the next 8

File: LED.kicad_sch Sheet: /LED/ C18

logic of the LEDs (min 0.7*VDD for V_IH). All the

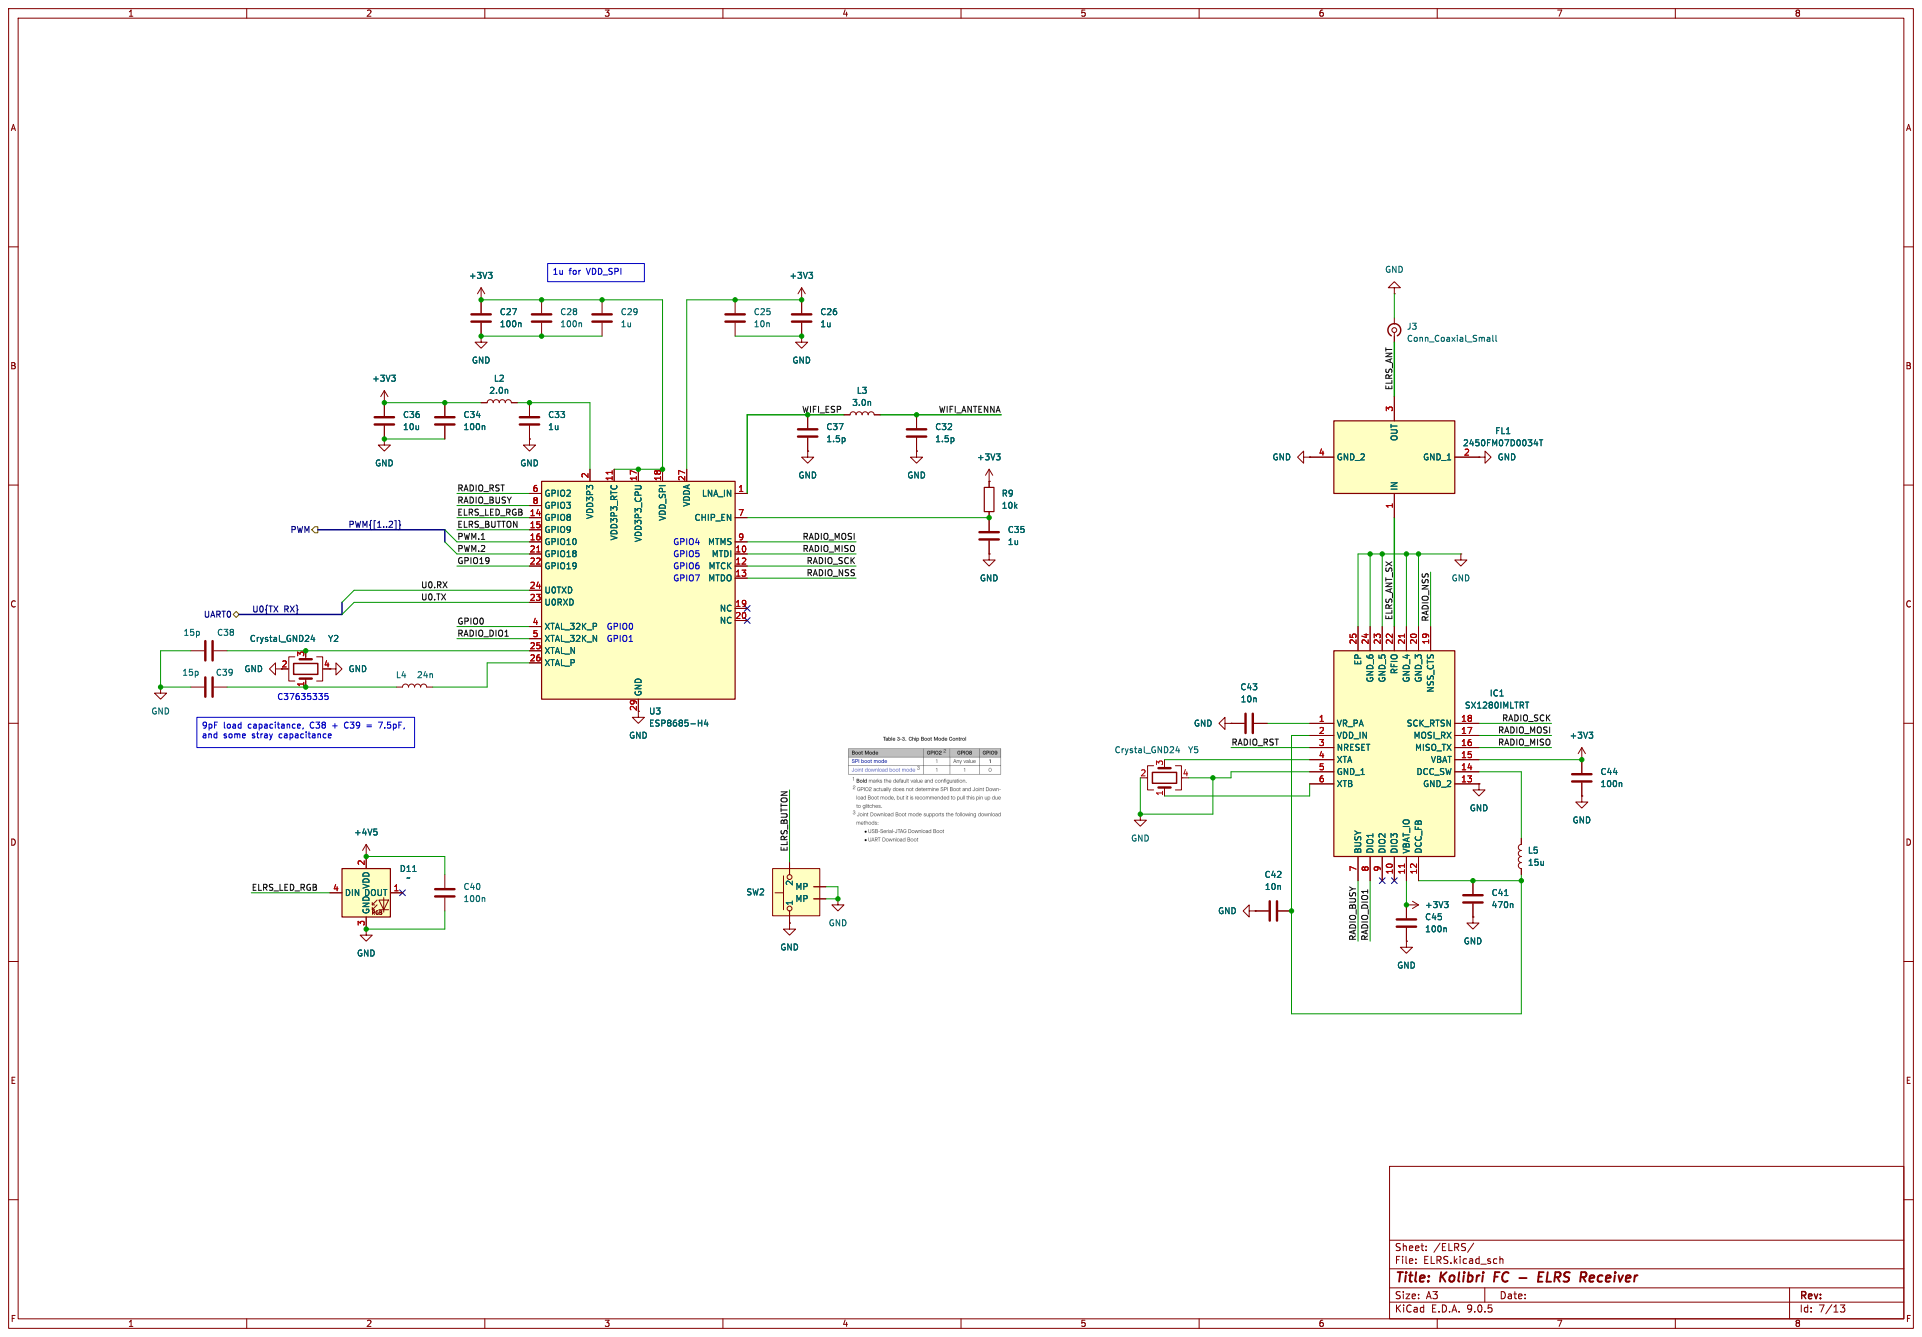
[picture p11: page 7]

LNA_IN 1 CHIP_EN 7 MTMS 9 MTDI 10 MTCK 12 MTDO 13 NC 19 NC 20 U3ESP8685-H4

3 GND GND GND GND

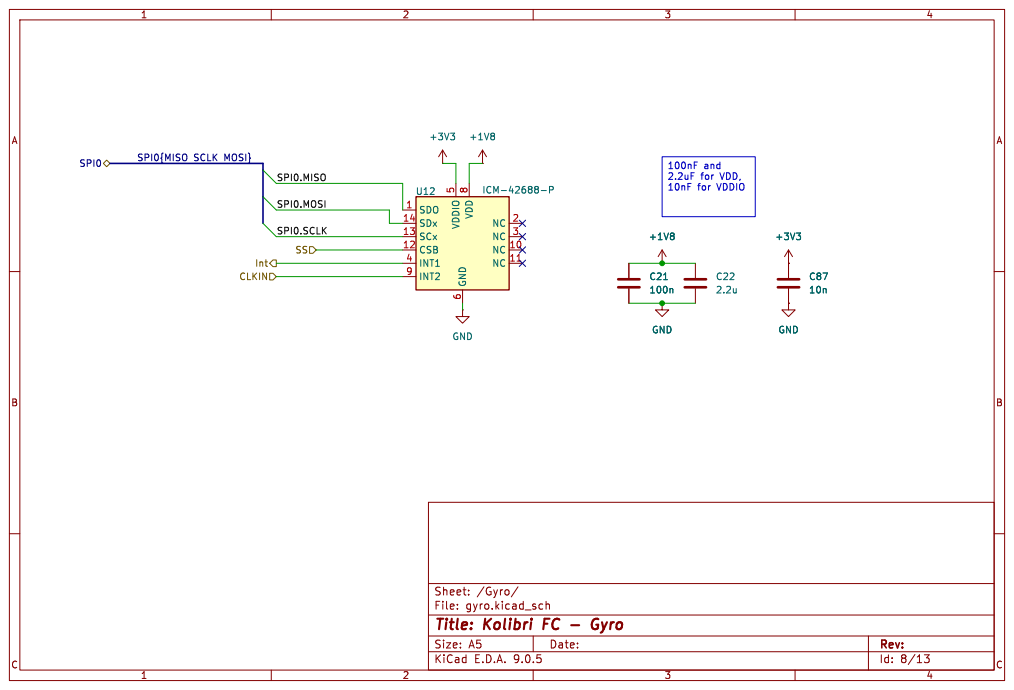
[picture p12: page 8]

8 NC 2 NC 3 NC 10 NC 11 U12 ICM-42688-P GND GND

2.2uF for VDD, 10nF for VDDIO

Id: 8/13 Title: Kolibri FC - Gyro

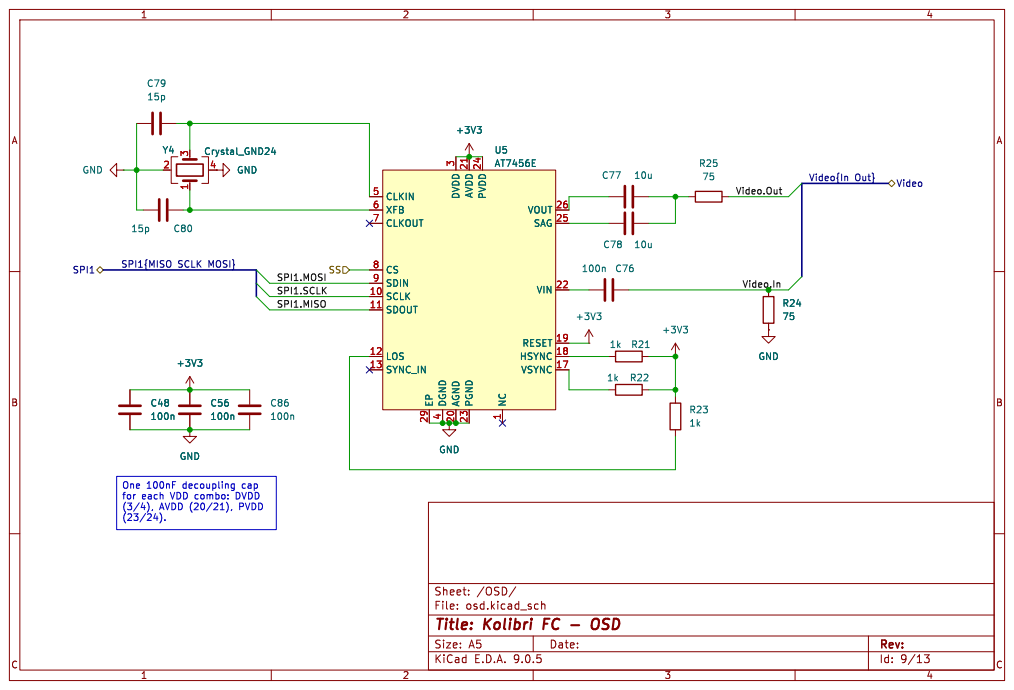
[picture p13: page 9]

1 VOUT 26 SAG 25 VIN 22 RESET 19 HSYNC 18 VSYNC 17 U5AT7456E

3 AGND 20 AVDD 21 PGND 23 PVDD 24 NC

1 VOUT 26 SAG 25 VIN 22 RESET 19 HSYNC 18 VSYNC 17 GND

for each VDD combo: DVDD

Id: 9/13 Title: Kolibri FC - OSD

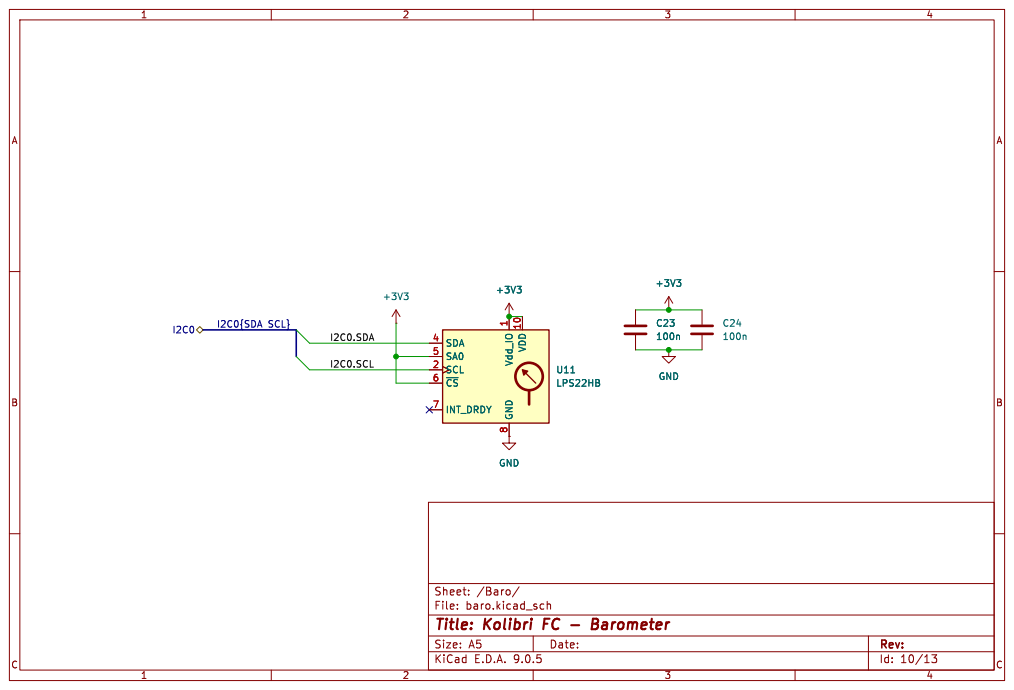
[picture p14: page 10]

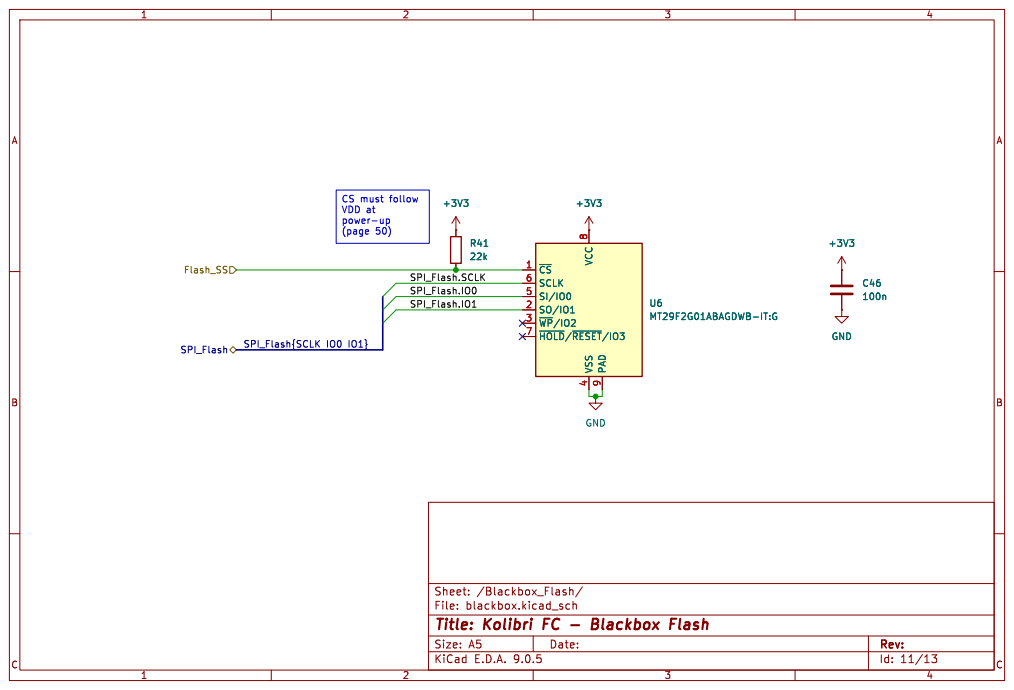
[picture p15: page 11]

SPI_Flash.IO0 CS must follow
VDD at power-up

Id: 11/13 Title: Kolibri FC - Blackbox Flash

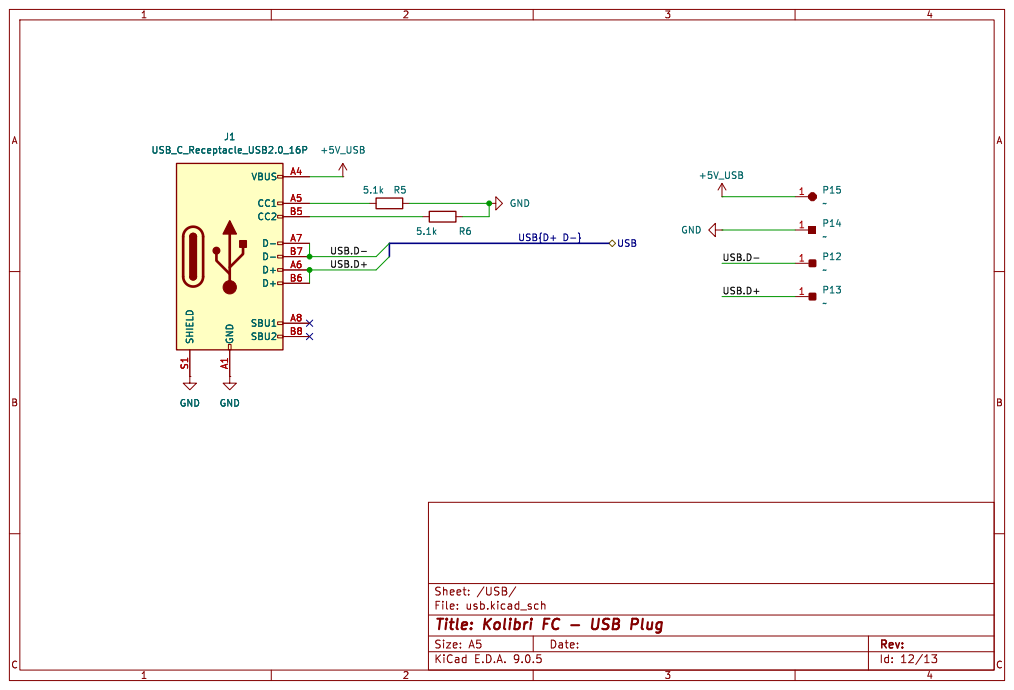
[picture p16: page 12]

File: usb.kicad_sch Sheet: /USB/
Id: 12/13 Title: Kolibri FC - USB Plug


Emergency diode for if that happens during flight.

File: power.kicad_sch Sheet: /Power/
Id: 13/13 Title: Kolibri FC - DCDC + LDO










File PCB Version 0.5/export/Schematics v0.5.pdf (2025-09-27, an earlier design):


I2C0 Baro File: baro.kicad_schVideo UART0 Motors
Gyro_Int SWD

Int Gyro File: gyro.kicad_sch

Id: 1/13 Title: File: Kolibri v0.5.kicad_sch Sheet: /


{SWDIO SWCLK} U10 W25Q16JVUXIQ
IO3 7 VCC
~{CS}1 CLK 6 DI(IO0) 5 DO(IO1) 2

SPI1{MISO SCLK MOSI} SPI1.SCLK

Id: 2/13 Title: Kolibri FC - RP2350 Schematics


ELRS PWM outputs
Video.Out PWM.2 PWM.4
PWM.3 SWDIO

Video.In PWM.1 U0.TX U0.RX

File: connectors.kicad_sch Sheet: /Connectors/ GND

Id: 3/13 Title: Kolibri FC - External Connections


JP1 SolderJumper_3_Open

Id: 4/13 Title: Kolibri FC - Speaker Driver File: speaker.kicad_sch Sheet: /Speaker/ 1


File: ADC.kicad_sch Sheet: /ADC/ R27

Id: 5/13 Title: Kolibri FC - ADC Buffers


File: LED.kicad_sch Sheet: /LED/ +5V D14

its second use is a level shifter for the next 8

logic of the LEDs (min 0.7*VDD for V_IH). All the


1u caps for VDD_SDIO and VDDA (pin 43 or 46), 100n for all other pins
U0.TX RADIO_SCK RADIO_MOSI
LED_RGB RADIO_MISO

1 2 MP MP SW2 GND GND


between VDDIO
and GNDIO and
one between VDD and GND

7 ASDx 2 ASCx 3 OCSB 10 OSDO 11 U2BMI270 C21

7 ASDx 2 ASCx 3 OCSB 10 OSDO 11 +3V3

Id: 8/13 Title: Kolibri FC - Gyro


1 VOUT 26 SAG 25 VIN 22 RESET 19 HSYNC 18 VSYNC 17 U5AT7456E

3 AGND 20 AVDD 21 PGND 23 PVDD 24 NC

1 VOUT 26 SAG 25 VIN 22 RESET 19 HSYNC 18 VSYNC 17 GND

for each VDD combo: DVDD

Id: 9/13 Title: Kolibri FC - OSD



File: sd.kicad_sch Sheet: /SD/
Id: 11/13 Title: Kolibri FC - Blackbox Micro SD


5 2 U8 WE-TVS-824015043 GND GND GND SHIELD S1 GND A1 VBUS A4 CC1 A5 CC2 B5 D- A7 D- B7 D+ A6 D+ B6 SBU1 A8 SBU2 B8

File: usb.kicad_sch Sheet: /USB/
Id: 12/13 Title: Kolibri FC - USB Plug


Emergency diode for if that happens during flight.

1 VOUT 2 ST 8 GND GND

separate 3.3V supply. Both LDOs have an almost identical pinout where only PG and GND are swapped, but because both

File: power.kicad_sch Sheet: /Power/
Id: 13/13 Title: Kolibri FC - DCDC + LDO

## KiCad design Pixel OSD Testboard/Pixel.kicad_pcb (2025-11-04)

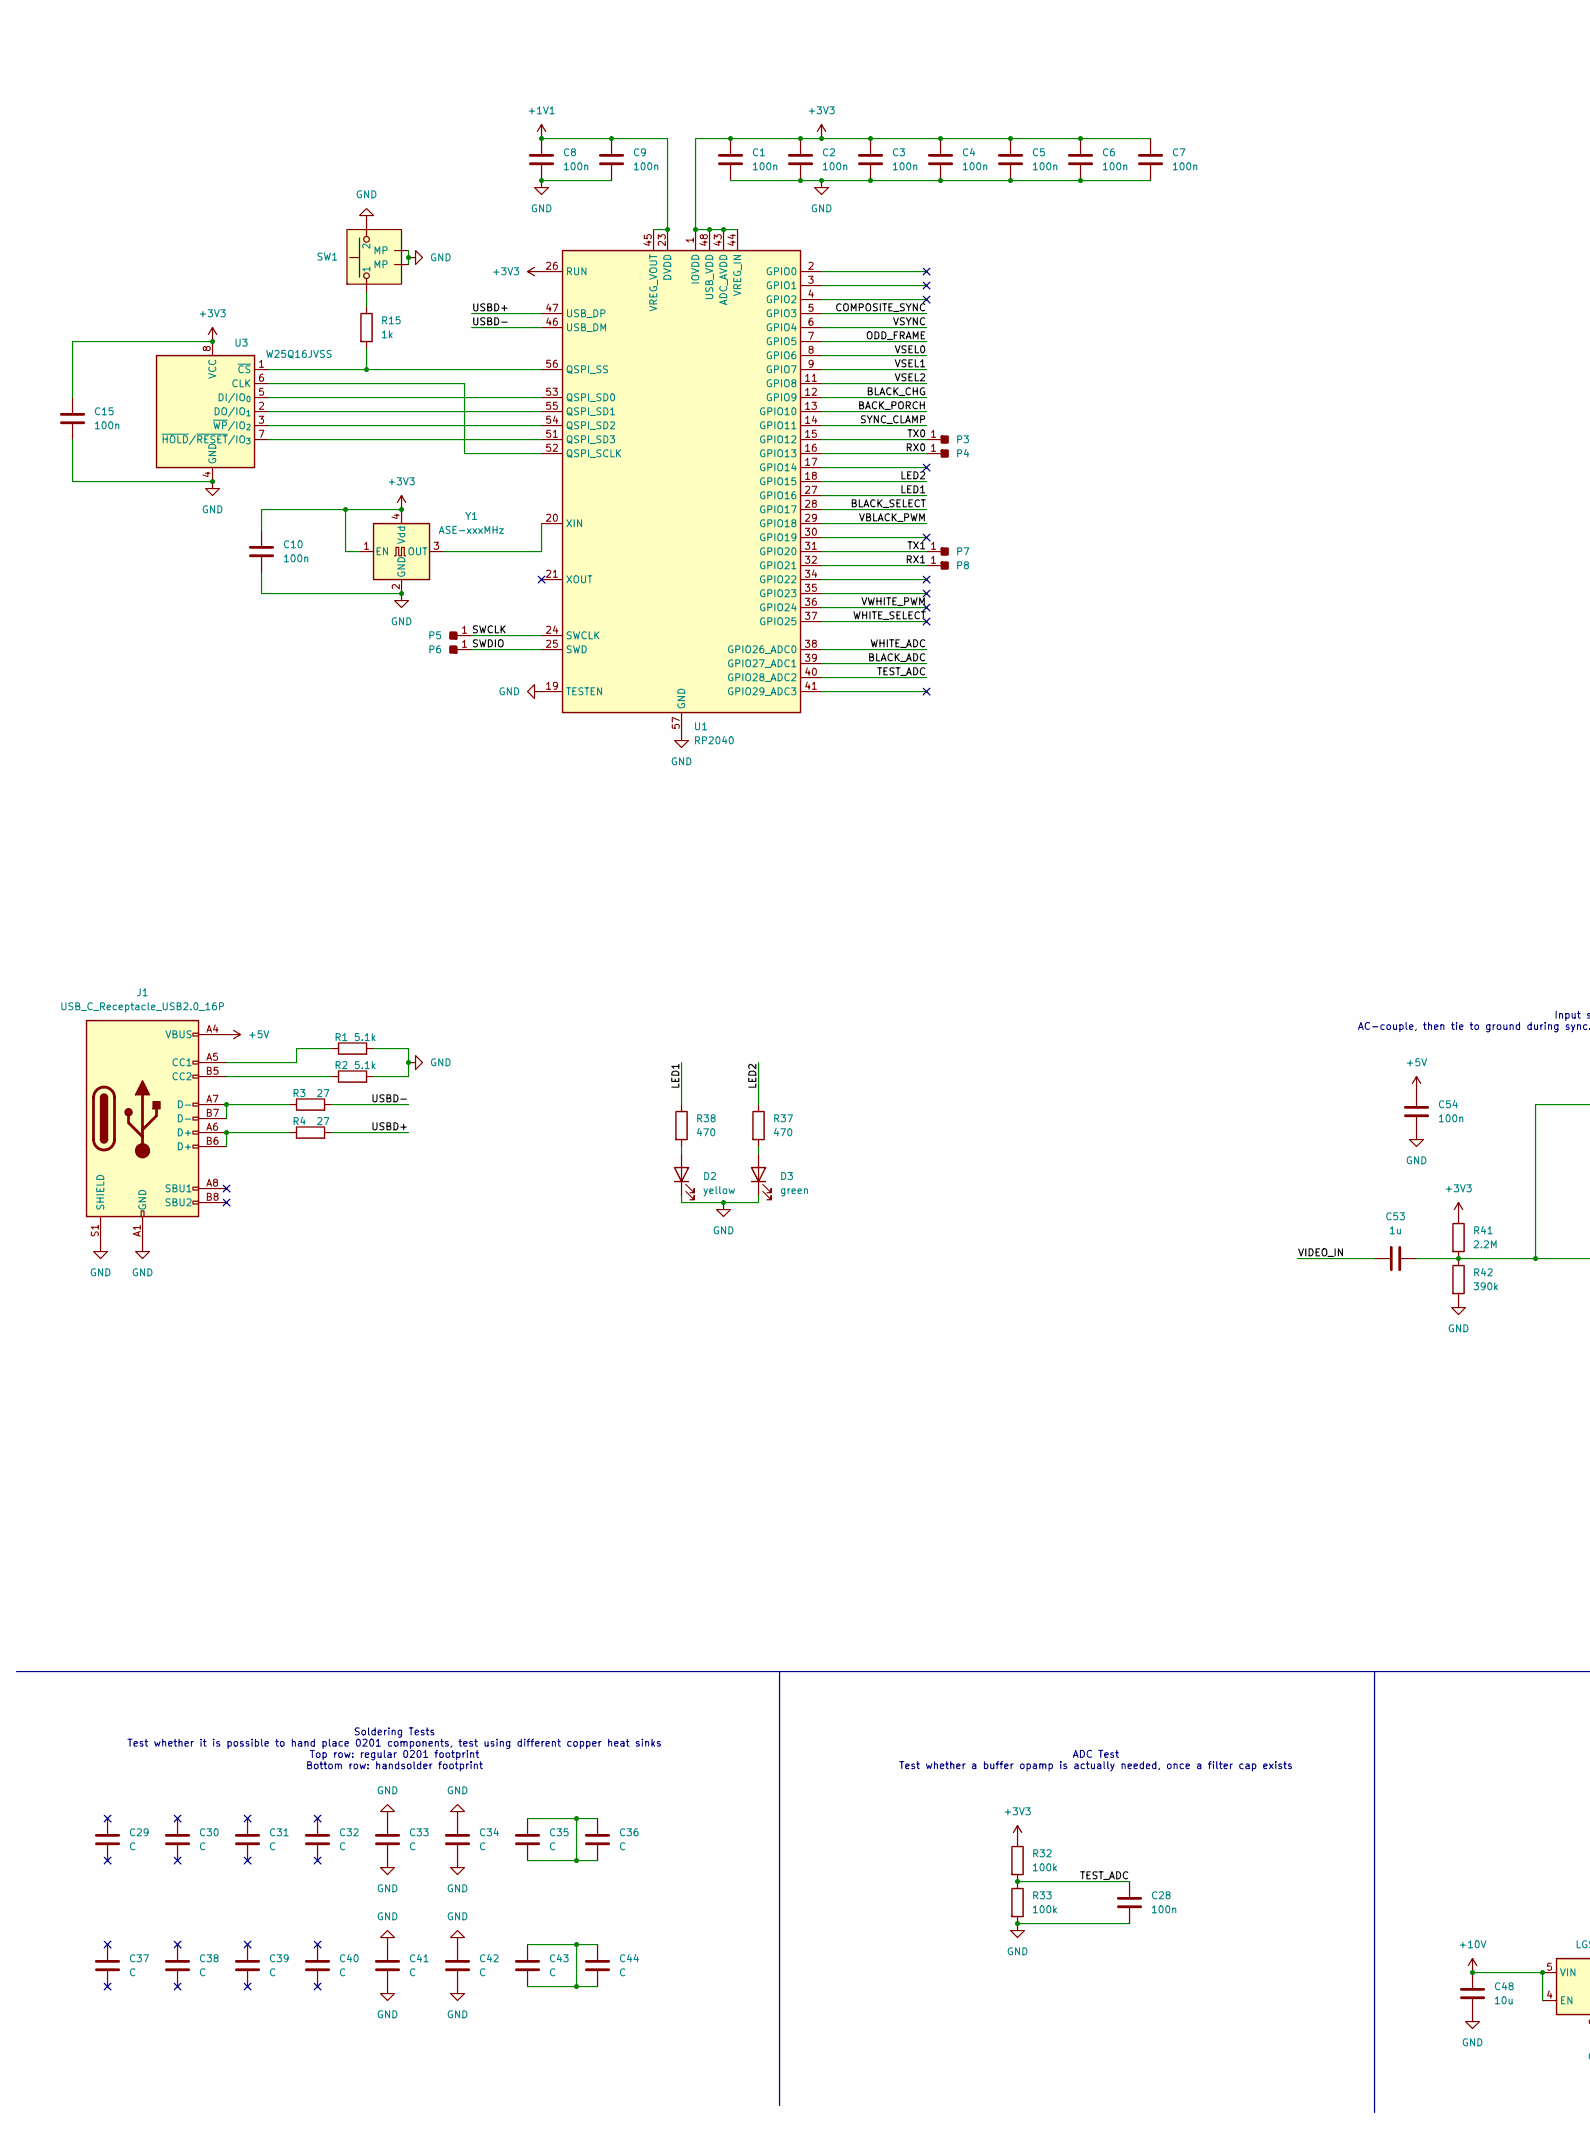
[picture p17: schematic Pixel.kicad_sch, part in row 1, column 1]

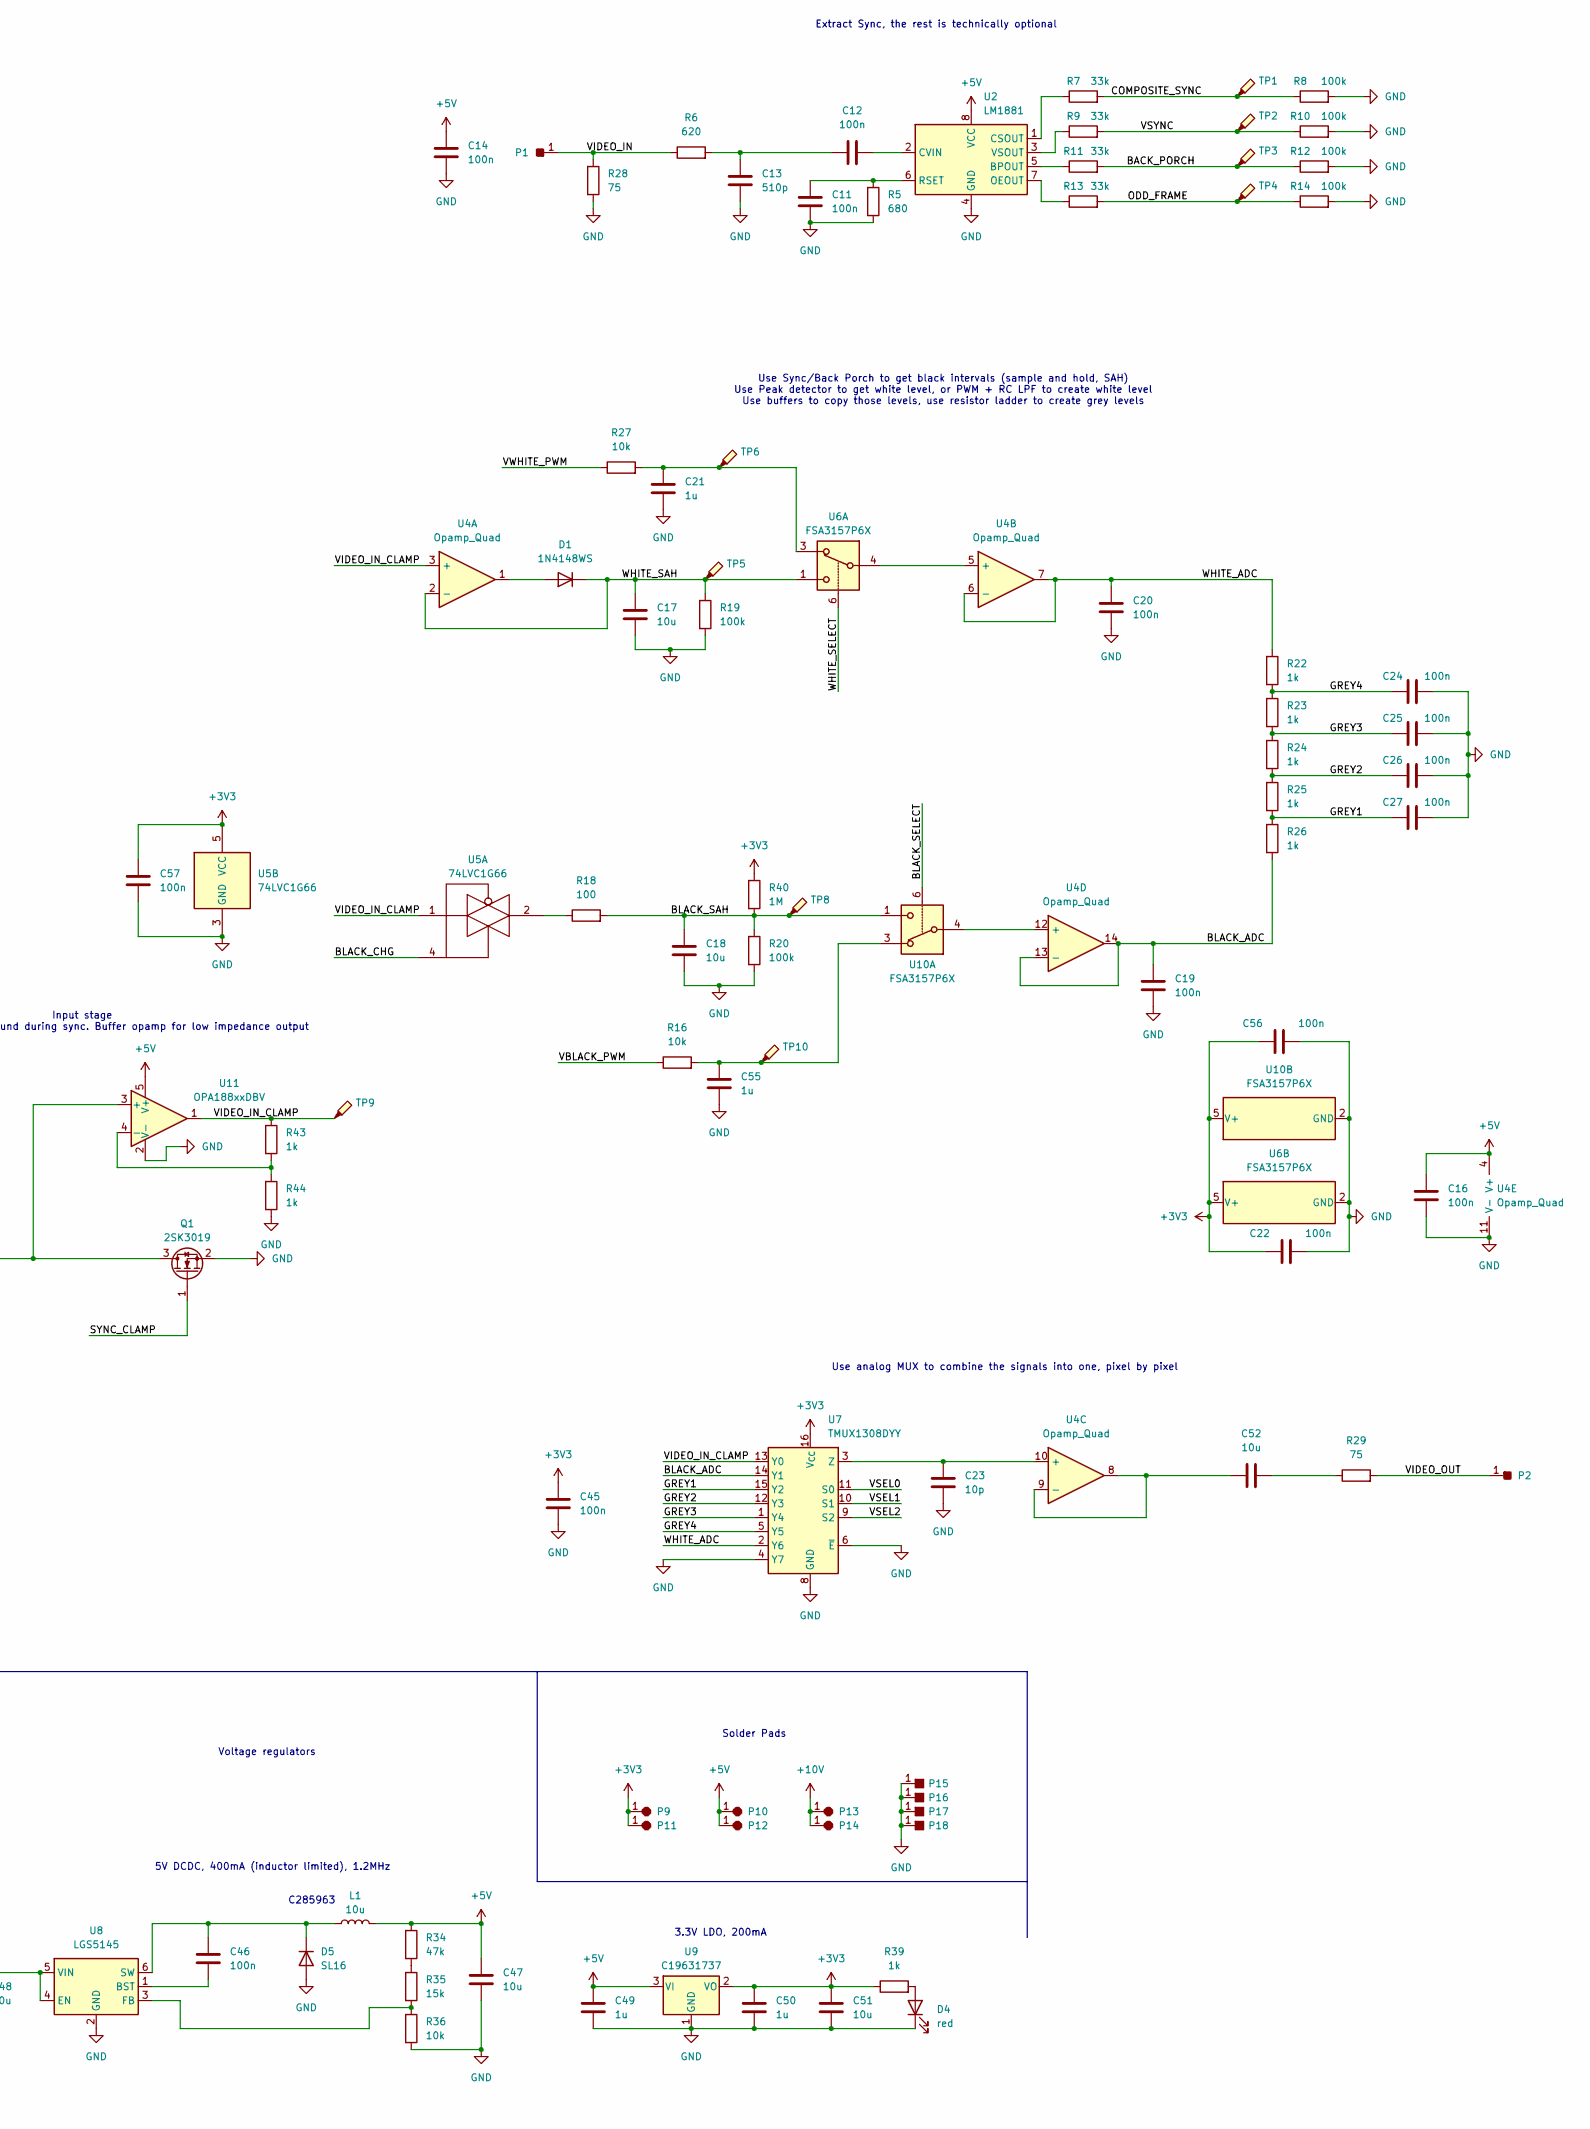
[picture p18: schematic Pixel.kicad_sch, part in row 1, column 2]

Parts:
C1, C2, C3, C4, C5, C6, C7, C8, C9, C10, C14, C15, C16, C19, C20, C22, C28, C45, C46, C54, C56, C57: 100n; C_0402_1005Metric
C11, C12: 100n; C_0603_1608Metric_Pad1.08x0.95mm_HandSolder
C13: 510p; C_0603_1608Metric_Pad1.08x0.95mm_HandSolder
C17, C18, C52: 10u; C_0603_1608Metric_Pad1.08x0.95mm_HandSolder
C21, C49, C50, C55: 1u; C_0402_1005Metric
C23: 10p; C_0402_1005Metric_Pad0.74x0.62mm_HandSolder
C24, C25, C26, C27: 100n; C_0402_1005Metric_Pad0.74x0.62mm_HandSolder
C29, C30, C31, C32, C33, C34, C35, C36: C; C_0201_0603Metric
C37, C38, C39, C40, C41, C42, C43, C44: C; C_0201_0603Metric_Pad0.64x0.40mm_HandSolder
C47, C51: 10u; C_0402_1005Metric
C48: 10u; C_0603_1608Metric
C53: 1u; C_0603_1608Metric_Pad1.08x0.95mm_HandSolder
D1: 1N4148WS; D_SOD-323
D2: yellow; LED_0603_1608Metric
D3: green; LED_0603_1608Metric
D4: red; LED_0603_1608Metric
D5: SL16; D_SOD-123
J1: USB_C_Receptacle_USB2.0_16P; USB-C SMD+THT
L1: 10u; L_0805_2012Metric
P1, P2, P3, P4, P5, P6, P7, P8: Solder_Pad_rounded
P9, P10, P11, P12, P13, P14: Solder_Pad_octa
P15, P16, P17, P18: Solder_Pad_rect
Q1: 2SK3019; SOT-523
R1, R2: 5.1k; R_0402_1005Metric
R3, R4: 27; R_0402_1005Metric
R5: 680; R_0603_1608Metric_Pad0.98x0.95mm_HandSolder
R6: 620; R_0603_1608Metric_Pad0.98x0.95mm_HandSolder
R7, R9, R11, R13: 33k; R_0402_1005Metric_Pad0.72x0.64mm_HandSolder
R8, R10, R12, R14: 100k; R_0402_1005Metric_Pad0.72x0.64mm_HandSolder
R15, R39: 1k; R_0402_1005Metric
R16, R27, R36: 10k; R_0402_1005Metric
R18: 100; R_0603_1608Metric_Pad0.98x0.95mm_HandSolder
R19, R20: 100k; R_0603_1608Metric_Pad0.98x0.95mm_HandSolder
R22, R23, R24, R25, R26, R43, R44: 1k; R_0603_1608Metric_Pad0.98x0.95mm_HandSolder
R28, R29: 75; R_0402_1005Metric
R32, R33: 100k; R_0402_1005Metric
R34: 47k; R_0402_1005Metric
R35: 15k; R_0402_1005Metric
R37, R38: 470; R_0402_1005Metric
R40: 1M; R_0603_1608Metric_Pad0.98x0.95mm_HandSolder
R41: 2.2M; R_0603_1608Metric_Pad0.98x0.95mm_HandSolder
R42: 390k; R_0603_1608Metric_Pad0.98x0.95mm_HandSolder
SW1: Button C530669
TP1, TP2, TP3, TP4, TP5, TP6, TP8, TP9, TP10: TestPoint_Probe; TestPoint_Pad_D1.0mm
U1: RP2040; QFN-56-1EP_7x7mm_P0.4mm_EP3.2x3.2mm
U2: LM1881; SOIC-8_3.9x4.9mm_P1.27mm
U3: W25Q16JVSS; SOIC-8_5.3x5.3mm_P1.27mm
U4: Opamp_Quad; TSSOP-14_4.4x5mm_P0.65mm
U5: 74LVC1G66; SOT-353_SC-70-5
U6, U10: FSA3157P6X; SOT-363_SC-70-6
U7: TMUX1308DYY; Texas_DYY0016A_TSOT-23-16_2x4.2mm_P0.5mm
U8: LGS5145; SOT-23-6
U9: C19631737; SOT-23-3
U11: OPA188xxDBV; TSOT-23-5
Y1: ASE-xxxMHz; Oscillator_SMD_Abracon_ASE-4Pin_3.2x2.5mm_HandSoldering

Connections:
+1V1: C8.1, C9.1, U1.23 (DVDD), U1.45 (VREG_VOUT), U1.50 (DVDD)
+3V3: C1.1, C2.1, C3.1, C4.1, C5.1, C6.1, C7.1, C10.1, C15.1, C22.1, C45.1, C50.1, C51.1, C56.1, C57.1, P9.1, P11.1, R32.1, R39.1, R40.1, R41.1, U1.1 (IOVDD), U1.10 (IOVDD), U1.22 (IOVDD), U1.26 (RUN), U1.33 (IOVDD), U1.42 (IOVDD), U1.43 (ADC_AVDD), U1.44 (VREG_IN), U1.48 (USB_VDD), U1.49 (IOVDD), U3.8 (VCC), U5.5 (VCC), U6.5 (V+), U7.16 (V_{CC}), U9.2 (VO), U10.5 (V+), Y1.1 (EN), Y1.4 (Vdd)
+5V: C14.1, C16.1, C47.1, C49.1, C54.1, J1.A4 (VBUS), J1.A9 (VBUS), J1.B4 (VBUS), J1.B9 (VBUS), L1.2, P10.1, P12.1, R34.1, U2.8 (VCC), U4.4 (V+), U9.3 (VI), U11.5 (V+)
+10V: C48.1, P13.1, P14.1, U8.4 (EN), U8.5 (VIN)
/BACK_PORCH: R11.2, R12.1, TP3.1, U1.13 (GPIO10)
/BLACK_ADC: C19.1, R26.2, U1.39 (GPIO27_ADC1), U4.13 (-), U4.14, U7.14 (Y1)
/BLACK_CHG: U1.12 (GPIO9), U5.4
/BLACK_SAH: C18.1, R18.2, R20.1, R40.2, TP8.1, U10.1
/BLACK_SELECT: U1.28 (GPIO17), U10.6
/COMPOSITE_SYNC: R7.2, R8.1, TP1.1, U1.5 (GPIO3)
/GREY1: C27.1, R25.2, R26.1, U7.15 (Y2)
/GREY2: C26.1, R24.2, R25.1, U7.12 (Y3)
/GREY3: C25.1, R23.2, R24.1, U7.1 (Y4)
/GREY4: C24.1, R22.2, R23.1, U7.5 (Y5)
/LED1: R38.1, U1.27 (GPIO16)
/LED2: R37.1, U1.18 (GPIO15)
/ODD_FRAME: R13.2, R14.1, TP4.1, U1.7 (GPIO5)
/RX0: P4.1, U1.16 (GPIO13)
/RX1: P8.1, U1.32 (GPIO21)
/SWCLK: P5.1, U1.24 (SWCLK)
/SWDIO: P6.1, U1.25 (SWD)
/SYNC_CLAMP: Q1.1 (G), U1.14 (GPIO11)
/TEST_ADC: C28.1, R32.2, R33.1, U1.40 (GPIO28_ADC2)
/TX0: P3.1, U1.15 (GPIO12)
/TX1: P7.1, U1.31 (GPIO20)
/USBD+: R4.2, U1.47 (USB_DP)
/USBD-: R3.2, U1.46 (USB_DM)
/VBLACK_PWM: R16.1, U1.29 (GPIO18)
/VIDEO_IN: C53.1, P1.1, R6.1, R28.1
/VIDEO_IN_CLAMP: R43.1, TP9.1, U4.3 (+), U5.1, U7.13 (Y0), U11.1
/VIDEO_OUT: P2.1, R29.2
/VSEL0: U1.8 (GPIO6), U7.11 (S0)
/VSEL1: U1.9 (GPIO7), U7.10 (S1)
/VSEL2: U1.11 (GPIO8), U7.9 (S2)
/VSYNC: R9.2, R10.1, TP2.1, U1.6 (GPIO4)
/VWHITE_PWM: R27.1, U1.36 (GPIO24)
/WHITE_ADC: C20.1, R22.1, U1.38 (GPIO26_ADC0), U4.6 (-), U4.7, U7.2 (Y6)
/WHITE_SAH: C17.1, D1.1 (K), R19.1, TP5.1, U4.2 (-), U6.1
/WHITE_SELECT: U1.37 (GPIO25), U6.6
GND: C1.2, C2.2, C3.2, C4.2, C5.2, C6.2, C7.2, C8.2, C9.2, C10.2, C11.2, C13.1, C14.2, C15.2, C16.2, C17.2, C18.2, C19.2, C20.2, C21.2, C22.2, C23.2, C24.2, C25.2, C26.2, C27.2, C28.2, C33.1, C33.2, C34.1, C34.2, C41.1, C41.2, C42.1, C42.2, C45.2, C47.2, C48.2, C49.2, C50.2, C51.2, C54.2, C55.2, C56.2, C57.2, D2.1 (K), D3.1 (K), D4.1 (K), D5.2 (A), J1.A1 (GND), J1.A12 (GND), J1.B1 (GND), J1.B12 (GND), J1.S1 (SHIELD), P15.1, P16.1, P17.1, P18.1, Q1.2 (S), R1.2, R2.2, R5.2, R8.2, R10.2, R12.2, R14.2, R19.2, R20.2, R28.2, R33.2, R36.2, R42.2, R44.2, SW1.2, SW1.3 (MP), SW1.4 (MP), U1.19 (TESTEN), U1.57 (GND), U2.4 (GND), U3.4 (GND), U4.11 (V-), U5.3 (GND), U6.2 (GND), U7.4 (Y7), U7.6 (~E), U7.8 (GND), U8.2 (GND), U9.1 (GND), U10.2 (GND), U11.2 (V-), Y1.2 (GND)
unnamed: C12.1, C13.2, R6.2
unnamed: C21.1, R27.2, TP6.1, U6.3
unnamed: C35.1, C35.2, C36.1, C36.2
unnamed: C43.1, C43.2, C44.1, C44.2
unnamed: C52.2, R29.1
unnamed: C55.1, R16.2, TP10.1, U10.3
unnamed: D1.2 (A), U4.1
unnamed: D2.2 (A), R38.2
unnamed: D3.2 (A), R37.2
unnamed: D4.2 (A), R39.2
unnamed: C46.1, D5.1 (K), L1.1, U8.6 (SW)
unnamed: J1.A5 (CC1), R1.1
unnamed: J1.B5 (CC2), R2.1
unnamed: J1.A6 (D+), J1.B6 (D+), R4.1
unnamed: J1.A7 (D-), J1.B7 (D-), R3.1
unnamed: C53.2, Q1.3 (D), R41.2, R42.1, U11.3 (+)
unnamed: R15.1, SW1.1
unnamed: R18.1, U5.2
unnamed: R34.2, R35.1
unnamed: U1.52 (QSPI_SCLK), U3.6 (CLK)
unnamed: U1.53 (QSPI_SD0), U3.5 (DI/IO_{0})
unnamed: U1.55 (QSPI_SD1), U3.2 (DO/IO_{1})
unnamed: U1.54 (QSPI_SD2), U3.3 (~WP/IO_{2})
unnamed: U1.51 (QSPI_SD3), U3.7 (~HOLD/~RESET/IO_{3})
unnamed: R15.2, U1.56 (QSPI_SS), U3.1 (~CS)
unnamed: U1.20 (XIN), Y1.3 (OUT)
unnamed: R11.1, U2.5 (BPOUT)
unnamed: R7.1, U2.1 (CSOUT)
unnamed: C12.2, U2.2 (CVIN)
unnamed: R13.1, U2.7 (OEOUT)
unnamed: C11.1, R5.1, U2.6 (RSET)
unnamed: R9.1, U2.3 (VSOUT)
unnamed: U4.5 (+), U6.4
unnamed: C23.1, U4.10 (+), U7.3 (Z)
unnamed: C52.1, U4.8, U4.9 (-)
unnamed: U4.12 (+), U10.4
unnamed: C46.2, U8.1 (BST)
unnamed: R35.2, R36.1, U8.3 (FB)
unnamed: R43.2, R44.1, U11.4 (-)

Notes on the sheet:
Extract Sync, the rest is technically optional
3.3V LDO, 200mA
Soldering Tests Test whether it is possible to hand place 0201 components, test using different copper heat sinks Top row: regular 0201 footprint Bottom row: handsolder footprint
Solder Pads
5V DCDC, 400mA (inductor limited), 1.2MHz
ADC Test Test whether a buffer opamp is actually needed, once a filter cap exists
C285963
Input stage AC-couple, then tie to ground during sync. Buffer opamp for low impedance output
Voltage regulators
Use analog MUX to combine the signals into one, pixel by pixel
Use Sync/Back Porch to get black intervals (sample and hold, SAH) Use Peak detector to get white level, or PWM + RC LPF to create white level Use buffers to copy those levels, use resistor ladder to create grey levels

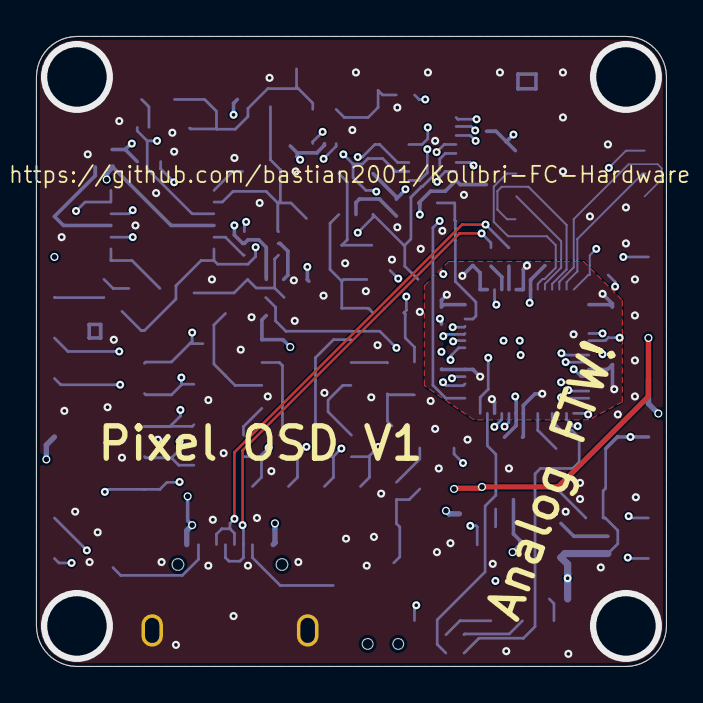
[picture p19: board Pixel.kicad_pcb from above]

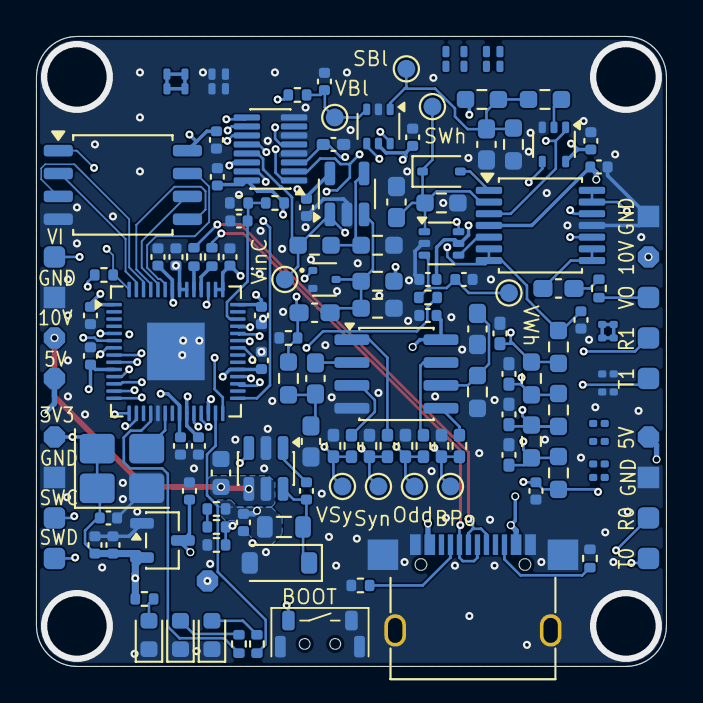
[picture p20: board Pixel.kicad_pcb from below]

Board: 6 copper layers, 35.0 x 35.0 mm, 145 parts (145 on the bottom side), 79 nets.

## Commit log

2025-09-27 PCB v0.2, not done yet
    still missing: Vias are untented, remove 0R resistors for voltage rails after v0.1 testing
    [Baro.SchDoc, Connectors.SchDoc, Custom Components.PcbLib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]
2025-09-27 Schematics PDF and solder rig for the stencil
    [Alignment card.prt, Alignment card.stl]
2025-09-27 some PCB v0.2 improvements
    [OSD.SchDoc, RP2040.SchDoc, Voltage Regulators.SchDoc]
2025-09-27 added pictures of board
    [PCB Version 0.1.PrjPcb, Voltage Regulators.SchDoc]
2025-09-27 updated changelog for PCB revisions
2025-09-27 v0.2 PCB ordered
    [Baro.SchDoc, Connectors.SchDoc, Flash.SchDoc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]
2025-09-27 moved simulations to "other"
    [INA139.DSN]
2025-09-27 first works on v0.3 pcb
    [Baro.SchDoc, Connectors.SchDoc, Custom Components.PcbLib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]
2025-09-27 PCB v0.3 wip - 0 rule violations, but not happy with routing
    [Baro.SchDoc, Connectors.SchDoc, Custom Components.PcbLib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]
2025-09-27 PCB version 0.3, see Cangelog.md
    [Main.SchDoc, PCB Version 0.3.PrjPcb, PCB Version 0.3.xlsx]
2025-09-27 V0.4 PCB
    hopefully fixes all the V0.3 issues:
    - ELRS range --> better grounding, RFX2401C
    - ELRS WiFi --> filter in front of antenna
    - ELRS crystal
    - ELRS boot button
    - I2C Pullups
    - OSD crystal trial and error
    - more spacing for 100nF caps
    [Baro.SchDoc, Connectors.SchDoc, Custom Components.PcbLib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]
2025-09-27 v0.4 as ordered, incl. exports (PDF, Gerber, BOM)
    [PCB Version 0.4.PrjPcb, PCB Version 0.4.xlsx]
2025-09-27 move solder rig where it belongs
    [Alignment card.prt, Alignment card.stl]
2025-09-27 Update voltage divider for power mux
    fixes 3.3V voltage drops due to the power switch switching too late after removing battery / too early when attaching battery
    [Voltage Regulators.SchDoc]
2025-09-27 add standalone ELRS RX (as ordered)
    [Custom Components.PcbLib, Custom Components.SchLib, ELRS Logic.SchDoc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]
2025-09-27 PCB version 0.5 (#56)
    [ADC.kicad_sch, BOM v0.5 pre.csv, BOM v0.5.csv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]
2025-09-27 move deprecated pcbs to deprecated
    [Alignment card.prt, Alignment card.stl, Baro.SchDoc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]
2025-10-07 PCB Version 0.6 (20mm FC) (#1)
    Changes compared to V0.5
    - ELRS from TD with PA/LNA to single without PA/LNA
    - ELRS from ESP32 to ESP8685 (C3)
    - Gyro from BMI270 to ICM-42688-P with external clock
    - Blackbox from SD slot to 2GBit flash chip
    - left it at RP2350A: 2354 unavailable and 2350B too large (and barely not needed)
    - No more separate ELRS LDO
    - Separate gyro LDO (1.8V – let's experiment!)
    - remove USB header in favor of solder pads
    - shrink Crystal footprints
    - remove USB TVS
    - replace current sensor pin with 10V reg switch
    [ADC.kicad_sch, BOM v0.6.csv, ELRS.kicad_sch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]
2025-11-04 Pixel OSD Testboard (#2)
    The goal of this board is to try to draw the OSD with the MCU itself. This would save BOM costs, reduce reliance on the AT7456E, and give more features like tighter OSD lines
    [Pixel-B_Cu.gbr, Pixel-B_Mask.gbr, Pixel-B_Paste.gbr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]
2025-11-10 added schematics and BOM for Pixel OSD Testboard
    [BOM Pixel.csv, BOM Pixel.ods, Pixel.kicad_sch]
